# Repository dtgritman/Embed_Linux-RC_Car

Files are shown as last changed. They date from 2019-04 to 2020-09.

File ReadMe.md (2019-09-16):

# Humans vs Zombies

### Team
 * **Miguel**: Building a vehicle to hold the project components.
 * **Dustin**: Building a nerf cannon that will angle up/down and rotate side to side. 
 * **Faizan**: Creating the object detection mechanism to target objects.

### Goal
 We plan to create a vehicle which shoots nerf projectiles for the campus-wide game called ‘Humans vs. Zombie’. Our tank has two hardware modules, the tanks enclosure and the nerf cannon used to fire the nerf pelts. We hope to add object recognition to our project to make it autonomous We will not only be using the Pi’s onboard GPIO pins but use a server to stream any video information onto a web-server. The Pi will also log anyone it deems to be threatening for correction or algorithm calibration.

# Tutorial 
Each part has its respective tutorial due to the modulization of the project. Please follow each markdown file closely and 

## Pi Setup

You can find a full tutorial in the [`setup/`](/setup/rasp_pi.md) folder

## Part 1 (Car Setup)

#### Modifications

1. Removing the top of the car 
2. Removing the cars microprocessor
3. Resoldering the on/off switch 

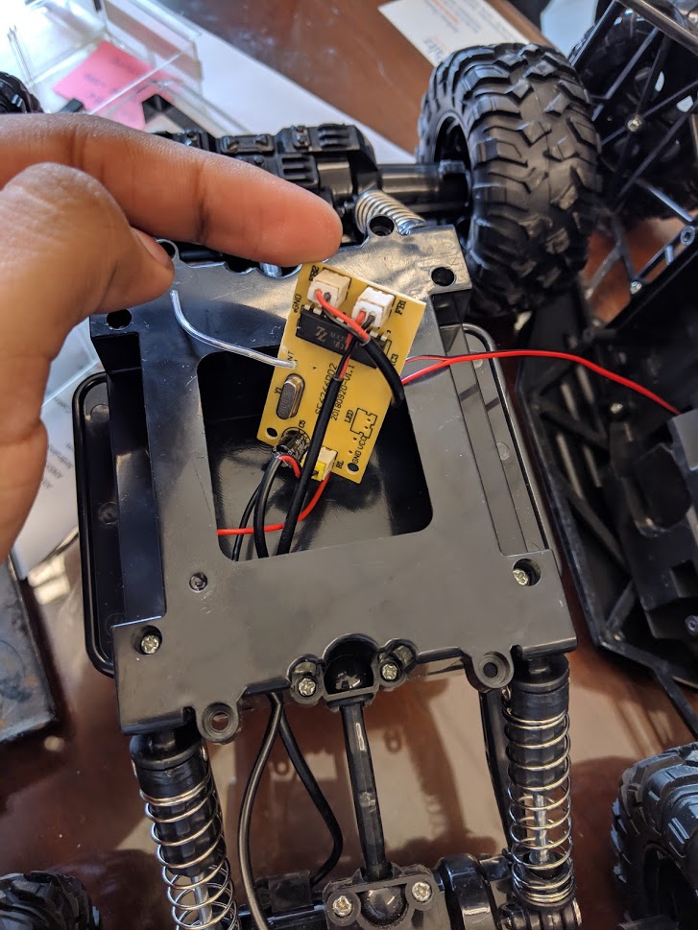
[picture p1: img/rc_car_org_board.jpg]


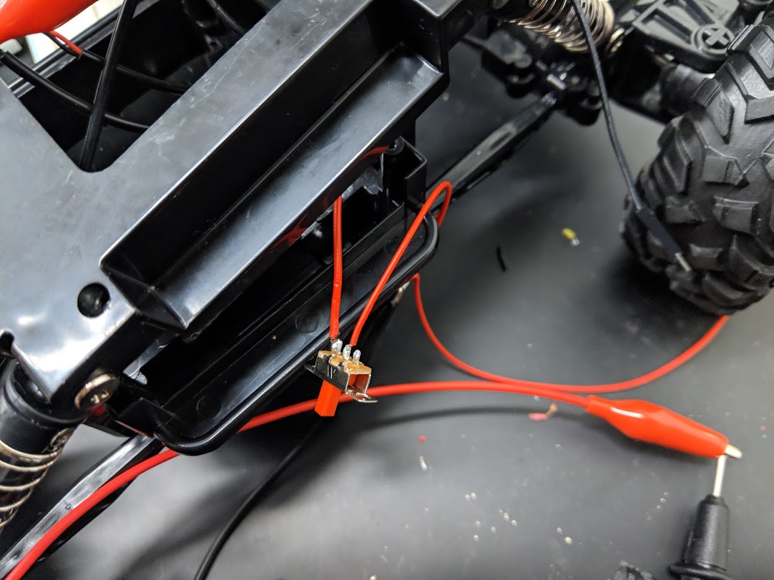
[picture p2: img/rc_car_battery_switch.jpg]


#### Wiring 

    STBY = GPIO #17     = Stand By

    Drive motor:
    PWMA = GPIO #3      = Speed
    AIN2 = GPIO #4
    AIN1 = GPIO #18

    Left-Right controller:
    BIN1 = GPIO #27
    BIN2 = GPIO #23    
    PWMB = GPIO #24    = Speed

## Part 2 (Nerf Module Setup)

Though this part can be completed without setting up the car we highly recommend finishing the car set-up for any changes you may need to make.

### Assembly of Cannon
#### Parts Needed
- Stepper Motor (NEMA 17)
- Standard 180 degree Servo Motor
- 1x Bearing (for the top stand center) with an inner diamter of 12mm, an outer diameter of 37mm, and a width of 12mm.
- 2x Bearings (for arm mounts) with an inner diameter of 7mm, outer diameter of 19mm, and a width of 6mm.
- 4x Transfer Ball bearings (for the legs of the top) with a bearing surface that has a diameter of 15mm and a mounting cylinder with a diameter of 25mm which has a flared top.

#### Stand Assembly
1. Sand the bearing mounting hole at the top of the arm until you can press in the bearing using a tool like a c-clamp (the bearing should not be able to be inserted by hand).
2. Once the bearing is mounted, insert the ArmAxle in to the bearing (some sanding may be required), this should be very difficult to insert and can be tapped in very lightly with a hammer.
3. With the ArmAxle mounted, you can place the ArmGear on the side with the stepper motor mount. This gear should be relatively difficult to push on the axle.
4. Place the stepper motor on the mount and screw it down but leave enough slack to slide the motor up and down.
5. Put the StepperGear on the motor and place it so the gears are in contact (leave a very small amount of space so the gears don't bind).
6. Push the LaserBracket on to the Axle (should be relatively snug).
7. Finally with the laser pointer mounted on the LaserRail, slide the rail in to the bracket (again this should be relatively snug).

#### Base Assembly
1. The base has raised wall which will be used to mount the ssd and raspberry pi, to do so we used velcro on the inner wall and ssd to mount it and on the outer wall we used neoprene closed cell foam to help hold the raspberry pi (and prevent damage to the pins) with rubber bands wrapped around.
2. With the bearing track sanded down, place the BaseGear on the center rod (should fit snuggly).

#### Top Assembly
1. First, press in the center bearing.
2. Attach the ServoGear to servo, we used hot glue on a servo horn (if using this method make sure its centered).
3. Mount the servo to the top using the ServoMounts (slowly screw the screws in, taking breaks frequently so you don't break screw).
4. Place the Transfer Ball Bearings in to the tops four arms (should fit snuggly).
5. Mount the stand(s) to the top using the ArmBrackets and ArmMounts (carefully screw in to the mounting holes).
6. Finally place the top on the base and press the top down so the base rod snuggly fits in the bearing and then place a screw through the TopBearingWasher and screw in to the rod to prevent the top from lifting off the base.

## Part 3 (Object Detection)

Our project uses OpenCV and python3 to detect human faces. We are using precompiled libraries. 
[Object Detection](/setup/object_detection.md)

## Part 4 (Putting it all together)

You can find our master init file in the [code/](https://github.com/MiguelAPerez/Humans-vs-Zombies/tree/master/code) folder. To run the RC Car run the `web.py` file using python3 

```bash
 $ python3 web.py
```

#### Citation 
 Cascade Used: [Opencv git repo](https://github.com/opencv/opencv/blob/master/data/haarcascades/haarcascade_frontalcatface.xml)

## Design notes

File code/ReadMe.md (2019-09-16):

## This folder contains all the code related to the project

All Pin values can be found in the `web.py` file

| File | Description |
|---|---|
| [Drone/Cannon.py](Drone/Cannon.py) | This file contains the TankCannon class and StepperMotor class which can be used to control the tanks cannon by turning it left, right, up, and down, and turning the cannon on and off. |
| [Drone/Car.py](Drone/Car.py) | This file contains the Car class which can be used to control the rc car drive and steering with speed control. |
| [web.py](web.py) | This program contains the webserver for the project which controls the tank. It uses Flask on port 8080. This also contains the detection code to run by itself. |
| [tankps4.py](tankps4.py) | This program can be used to control the tank with ps4 controller. (L2/R2 for drive, left joystick for steering, right joystick for cannon position, R1 for firing, and options to pause/resume) |
|[camera.py](camera.py)| Class for the video stream and object detection|

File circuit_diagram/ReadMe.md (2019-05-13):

# This directory contains the circuit diagrams for the car and the cannon

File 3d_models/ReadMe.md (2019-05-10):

# This directory has all the 3d models created and used for the project.
| 3D File | Notes |
| --- | ----- |
| [Arm.stl](Arm.stl) | The support arm (without a motor mount), will act as a support to help keep the nerf gun level with a bearing hole that fits an axle. |
| [ArmAxle.stl](ArmAxle.stl) | The axle connects the stands to the nerf gun mounting brackets (or laser mounting bracket), so they can rotate freely in a bearing. |
| [ArmAxleGear.stl](ArmAxleGear.stl) | This gear fits on the arm axle to mesh with the steppergear. |
| [ArmStand.stl](ArmStand.stl) | This stand has two sides that clamp the arms to hold them in place and connect them to the top. |
| [ArmStandMount.stl](ArmStandMount.stl) | This mount has holes and goes on the underside of the top for the arm stands to screw in. |
| [ArmStepper.stl](ArmStepper.stl) | The stepper arm for the nerf gun stand has a mount for the stepper motor (which will have a gear) and a hole for the axle bearing and the axle (which will also have a gear) to attach to the bracket of the nerf gun (or laser pointer) so the cannon can rotate. |
| [ArmStepperGear.stl](ArmStepperGear.stl) | This gear will slide on to the stepper motor and mesh with the axle gear to rotate the cannon. |
| [Base.stl](Base.stl) | The base will have the top slid on to rotate in the track. |
| [BaseGear.stl](BaseGear.stl) | This gear will be slid on the center pole to mesh with the servo gear. |
| [LaserMount.stl](LaserMount.stl) | The laser pointer will be connected to this mount. |
| [LaserMountBracket.stl](LaserMountBracket.stl) | The laser pointer mount will connect to this bracket which will connect to the arm axle. |
| [ServoGear.stl](ServoGear.stl) | This gear will be put on the servo horn and mesh with the base gear to rotate the top. |
| [ServoMount.stl](ServoMount.stl) | This mount goes on the top of the top and will have the servo screwed in. |
| [Top.stl](Top.stl) | The top will have the servo and arms mounted on it and then will be mounted to the base. |
| [TopBearingWasher.stl](TopBearingWasher.stl) | The washer will go between the center bearing in the top and the screw that will screw in to the base. |

## Extra Notes
##### - All 3D files were printed using a Standard Prusa i3 MK3 with the settings in Prusa Control of Detail: 0.1mm and Infill: around 20%
##### - Some sanding of parts will be required for them to fit together properly \*\*becareful not to remove too much material. They must fit snuggly\*\*

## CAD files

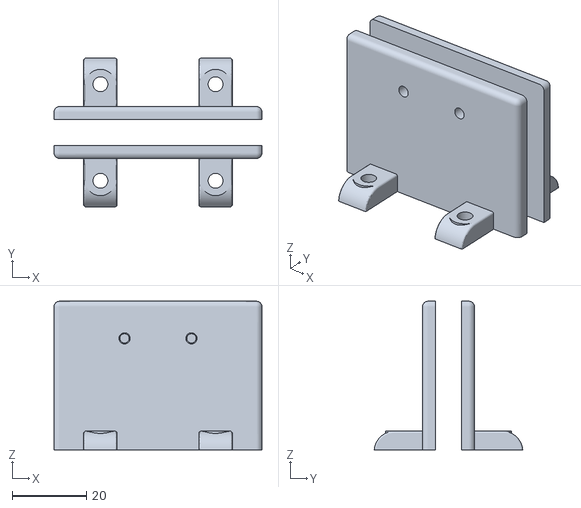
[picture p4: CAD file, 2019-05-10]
3d_models/ArmStand.stl
56.0 x 40.0 x 40.0

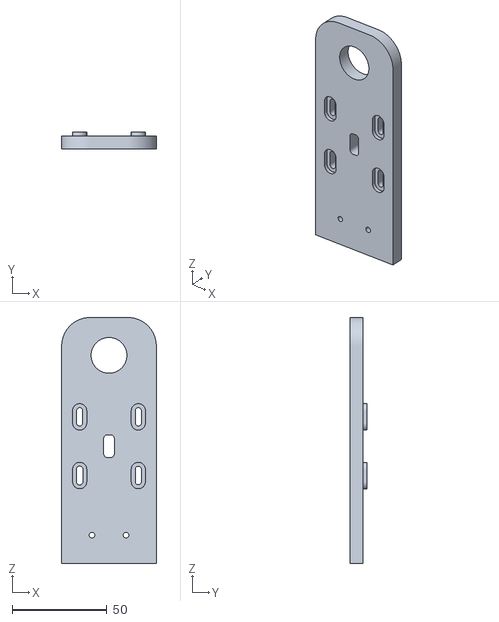
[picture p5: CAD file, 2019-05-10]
3d_models/ArmStepper.stl
50.0 x 9.00 x 130.0

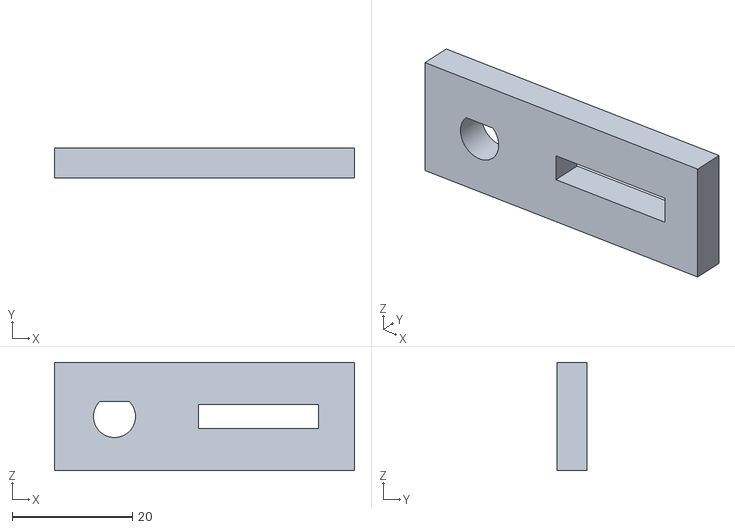
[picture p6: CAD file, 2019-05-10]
3d_models/LaserMountBracket.stl
50.0 x 5.00 x 18.0

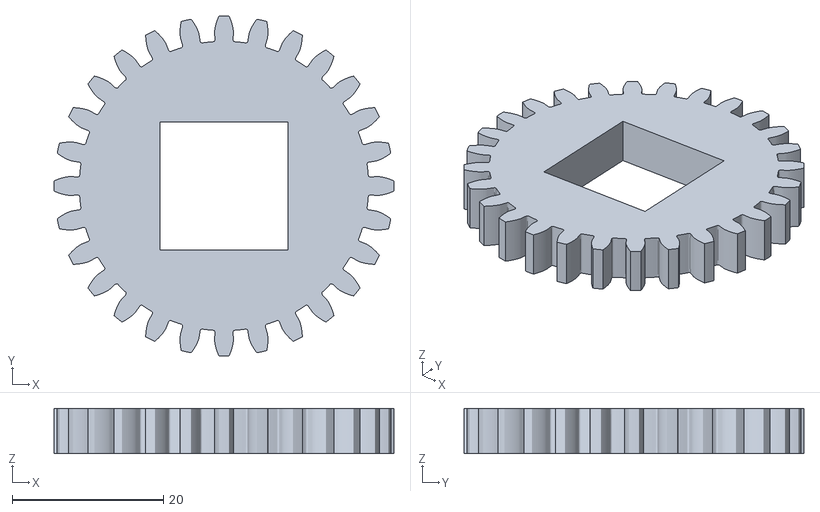
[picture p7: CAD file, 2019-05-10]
3d_models/BaseGear.stl
45.0 x 45.0 x 6.00

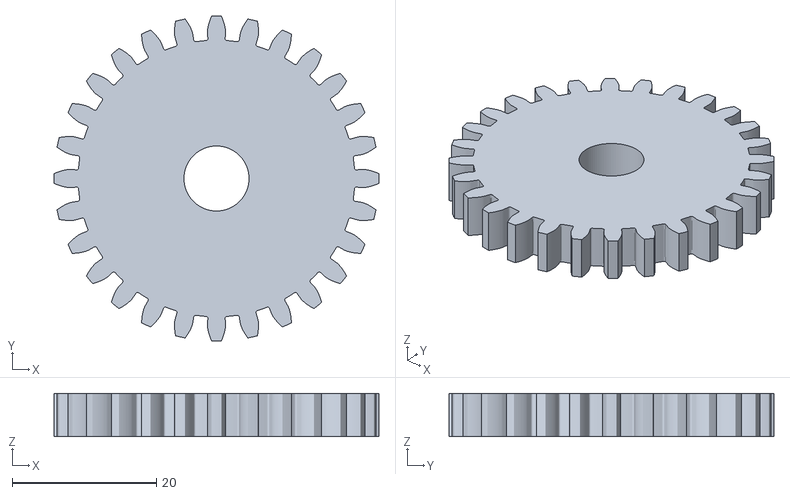
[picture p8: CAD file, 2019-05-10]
3d_models/ServoGear.stl
45.0 x 45.0 x 6.00

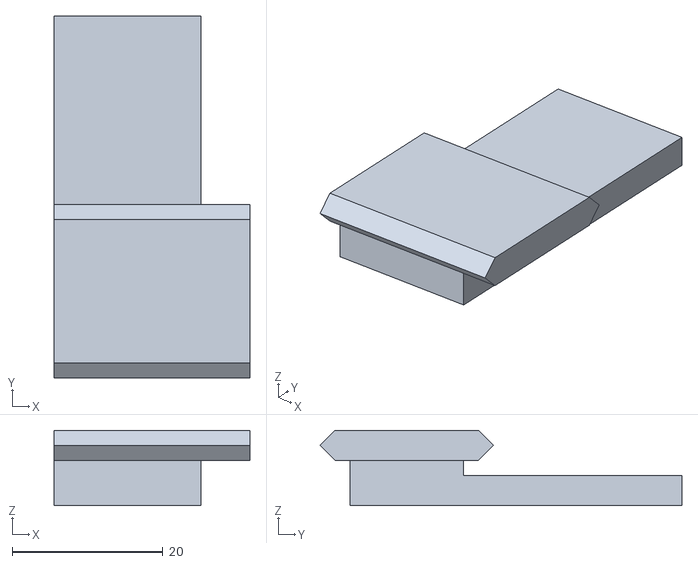
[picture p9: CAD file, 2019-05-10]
3d_models/LaserMount.stl
26.0 x 48.0 x 10.0

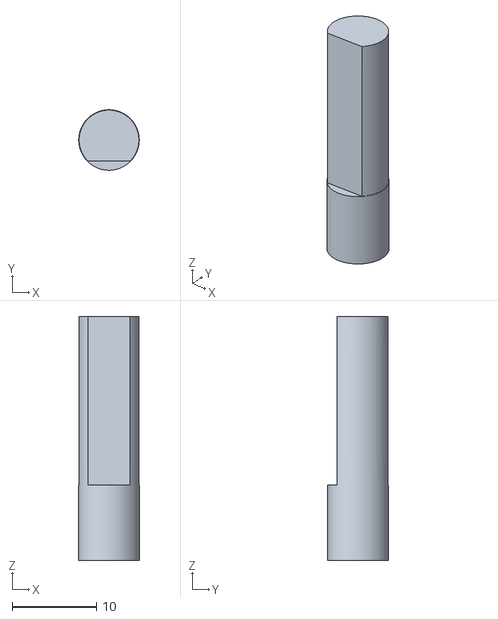
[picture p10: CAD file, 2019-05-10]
3d_models/ArmAxle.stl
7.20 x 7.20 x 29.0

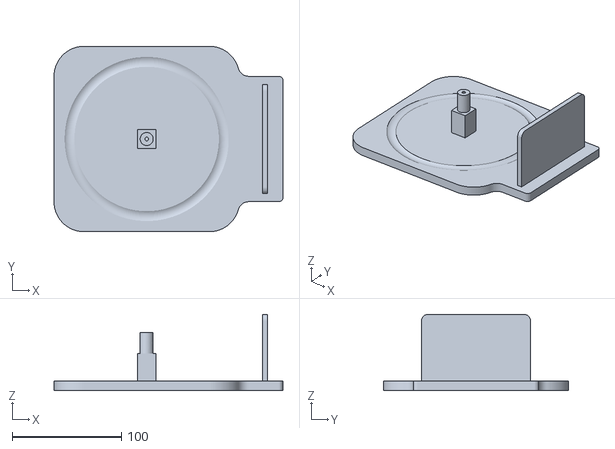
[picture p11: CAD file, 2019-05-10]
3d_models/Base.stl
210.0 x 170.0 x 70.0

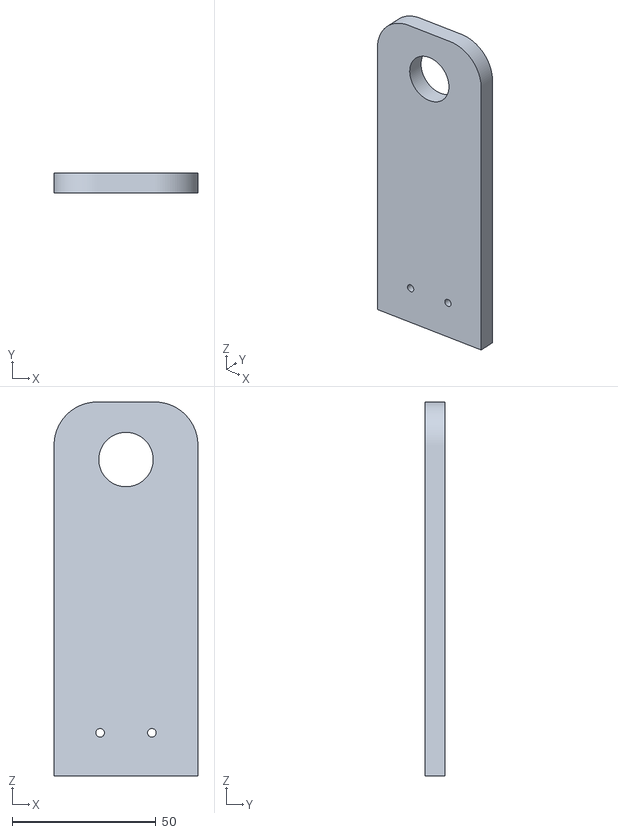
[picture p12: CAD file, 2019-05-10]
3d_models/Arm.stl
50.0 x 7.00 x 130.0

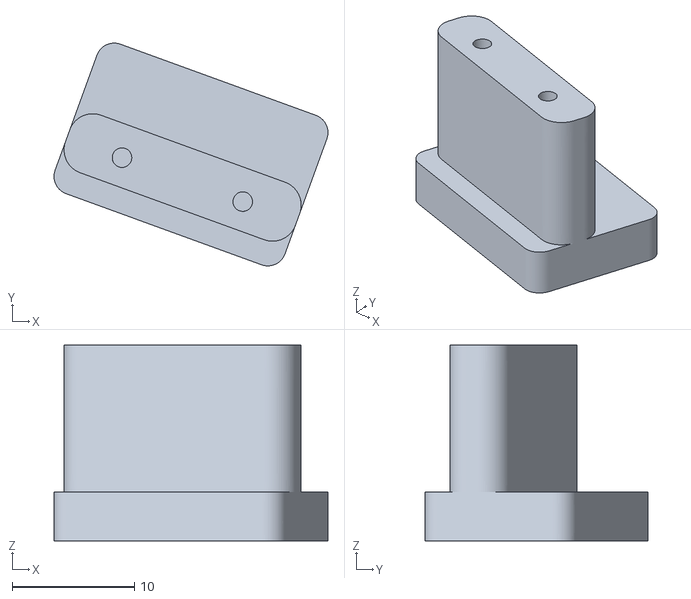
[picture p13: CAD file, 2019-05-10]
3d_models/ServoMount.stl
22.4 x 18.2 x 16.0

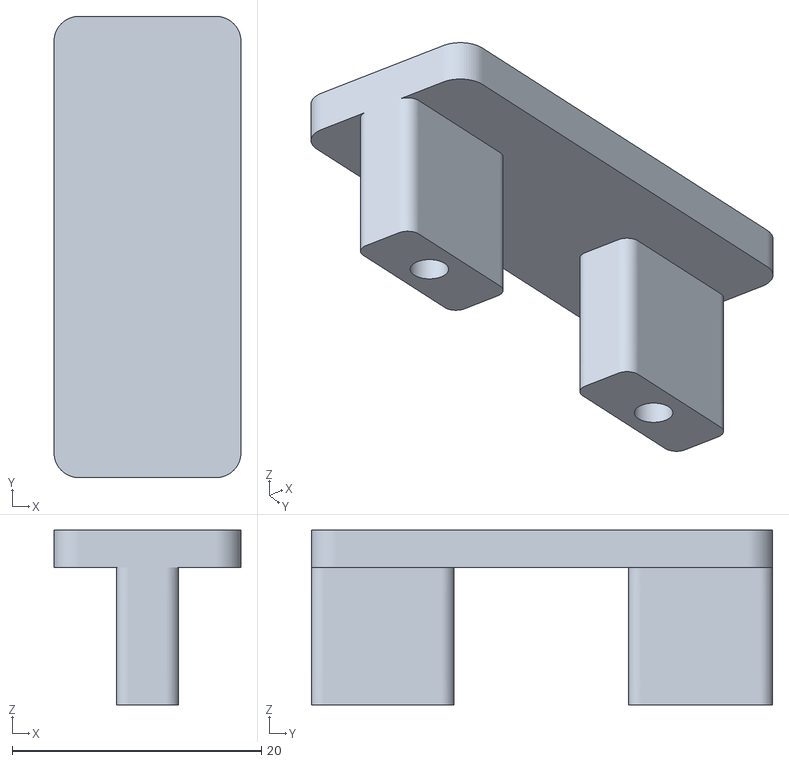
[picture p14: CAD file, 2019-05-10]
3d_models/ArmStandMount.stl
15.0 x 37.0 x 14.0

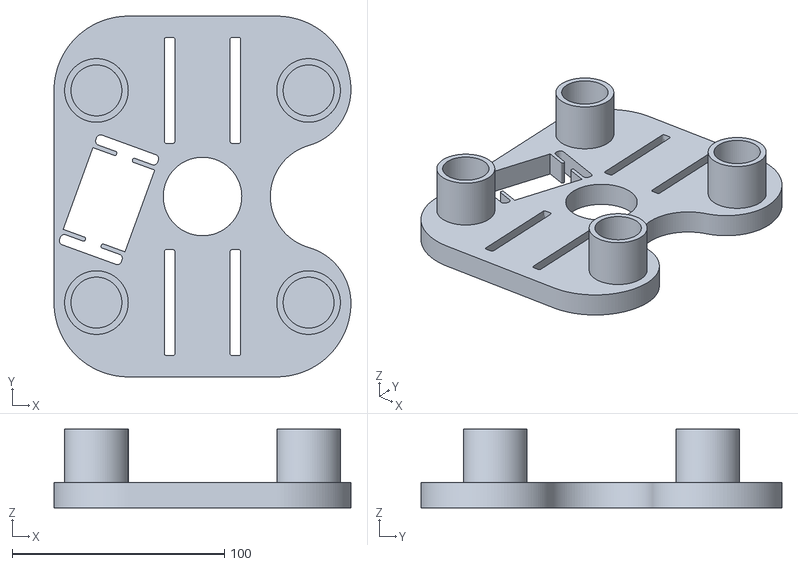
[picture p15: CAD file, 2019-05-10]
3d_models/Top.stl
140.0 x 170.0 x 37.0

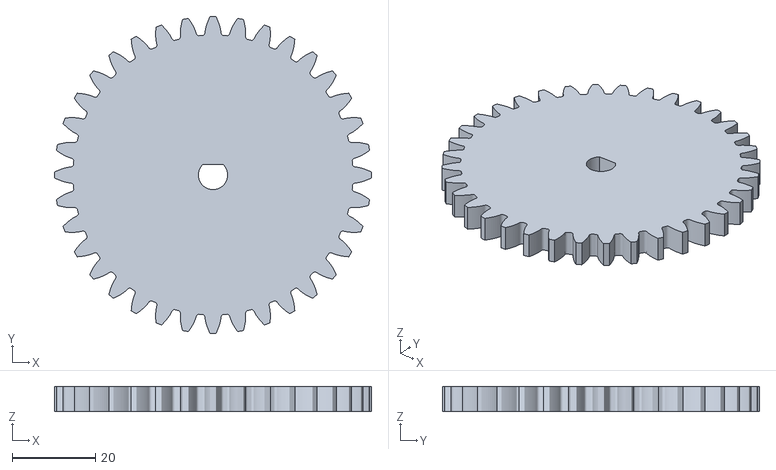
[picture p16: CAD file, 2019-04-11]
3d_models/ArmAxleGear.stl
76.0 x 76.0 x 6.00

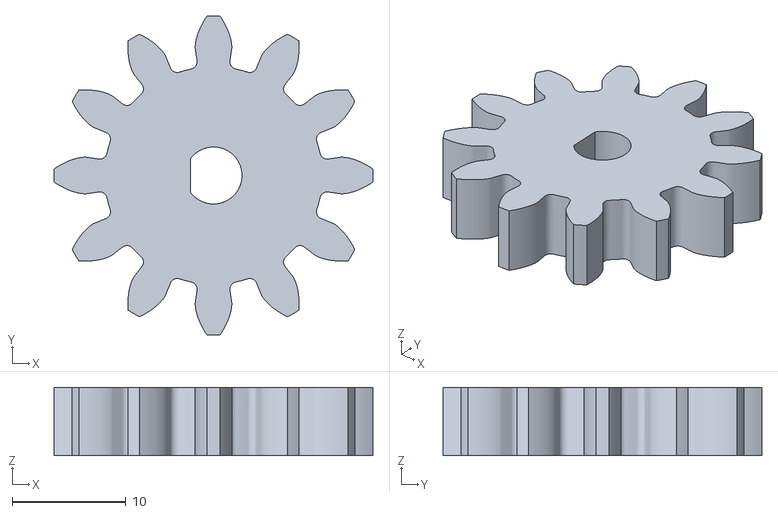
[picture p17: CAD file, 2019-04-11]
3d_models/ArmStepperGear.stl
28.0 x 28.0 x 6.00

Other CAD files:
3d_models/TopBearingWasher.stl

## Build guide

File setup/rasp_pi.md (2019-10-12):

## Setup 

Each part of the project is modularised for efficiency and fault prevention. This means each part (the nerf_module object_detection and rc_car) can work as a standalone part.  

### Raspberry Pi - Setup

Note that to execute these commands you need to open the terminal by finding it in the programs menu or by connecting a keyboard to the raspberry pi and pressing CTRL + ALT + T

Terminal- interface which lets you enter commands to perform tasks
sudo- command which gives a user more access to critical system files (equivalent of administrator privilages on Windows)
apt- the program that manages programs, allows you to install and remove programs
OpenCV- set of tools which allow you to work with videos and images, applications include facial recognition
Web server- computer which serves a web page to anyone connecting to it through the internet
Daemon- program that runs in the background
Static IP- IP address that does not change

##### Required Dependencies  
**Note:** You will need to have installed Raspbian or Raspbian Lite on your Pi.
If you don't know how to, follow the tutorial on the [Raspberry Pi Foundation's website](https://www.raspberrypi.org/documentation/installation/installing-images/)

The webserver uses flask. If it's not already installed the in can be installed with:  
```bash
$ sudo apt-get install python3-flask
```  
The tank control classes use pigpio to control the gpio. This library has better PWM signal control than RPi. To install this library use:  
```bash
$ sudo apt-get install pigpio python3-pigpio
```
This library requires the pigpio daemon to be running. This daemon can be started manually (only needs to be started once each boot) using:
```bash
$ sudo pigpiod
```
or it can be set to run on system boot with:
```bash
$ sudo systemctl enable pigpiod
$ sudo reboot
```

#### Hotspot Setup
We wanted to not be reliant on a router to connect to our Pi so we turned it into a hotspot to connect to it without our home or school wifi.

##### Access point in a standalone network (NAT)
**Note**: This is a short version of the raspberrypi.org tutorial. More information, it can be found [here](https://www.raspberrypi.org/documentation/configuration/wireless/access-point.md)

##### 1. Installs
Update your Pi
```bash
$ sudo apt-get update
$ sudo apt-get upgrade
```

Install all the required software:

```bash
$ sudo apt-get install dnsmasq hostapd
```

Turn the new software off as follows:
```bash
$ sudo systemctl stop dnsmasq
$ sudo systemctl stop hostapd
```

To ensure that an updated kernel is configured correctly after install, reboot:
```bash
$ sudo reboot 
```

##### 2. Configuring a static IP

This documentation assumes that we are using the standard 192.168.x.x IP addresses for our wireless network, so we will assign the server the IP address 192.168.4.1. It is also assumed that the wireless device being used is **wlan0**.

To configure the static IP address, edit the dhcpcd configuration file with:
```bash 
$ sudo nano /etc/dhcpcd.conf
```

Go to the end of the file and edit it so that it looks like:

```
interface wlan0
    static ip_address=192.168.4.1/24
    nohook wpa_supplicant
```
Now restart the dhcpcd daemon and set up the new wlan0 configuration:

```bash
$ sudo service dhcpcd restart
```
##### 3. Configuring the DHCP server (dnsmasq)

The DHCP service is provided by dnsmasq. By default, the configuration file contains a lot of information that is not needed, and it is easier to start from scratch. Rename this configuration file, and edit a new one:

```bash 
$ sudo mv /etc/dnsmasq.conf /etc/dnsmasq.conf.orig  
$ sudo nano /etc/dnsmasq.conf
```

Type or copy the following information into the dnsmasq configuration file and save it:
```
interface=wlan0      # Use the require wireless interface
  dhcp-range=192.168.4.2,192.168.4.20,255.255.255.0,24h
```
So for **wlan0**, we are going to provide IP addresses between 192.168.4.2 and 192.168.4.20, with a lease time of 24 hours. If you are providing DHCP services for other network devices (e.g. eth0), you could add more sections with the appropriate interface header, with the range of addresses you intend to provide to that interface.

##### 4. Configuring the access point host software (hostapd)

You need to edit the hostapd configuration file. After initial install, this will be a new/empty file.

```bash
$ sudo nano /etc/hostapd/hostapd.conf
```
Add the information below to the configuration file. This configuration assumes we are using channel 7, with a network name of **HumanVsZombies**, and a password **letmeinrightnow**. Note that the name and password should not have quotes around them. The passphrase should be between 8 and 64 characters in length.

```
interface=wlan0
driver=nl80211
ssid=HumanVsZombies
hw_mode=g
channel=7
wmm_enabled=0
macaddr_acl=0
auth_algs=1
ignore_broadcast_ssid=0
wpa=2
wpa_passphrase=letmeinrightnow
wpa_key_mgmt=WPA-PSK
wpa_pairwise=TKIP
rsn_pairwise=CCMP
```
We now need to tell the system where to find this configuration file.

```bash 
$ sudo nano /etc/default/hostapd
```
Find the line with #DAEMON_CONF, and replace it with this:
```
DAEMON_CONF="/etc/hostapd/hostapd.conf"
```

**Now start up the remaining services:**

```bash
$ sudo systemctl start hostapd
$ sudo systemctl start dnsmasq
```

**NOTE:** if sudo systemctl start hostapd fails to start and is masked you should use these commands to fix the issue:
```bash
$ sudo systemctl unmask hostapd
$ sudo systemctl enable hostapd
$ sudo systemctl start hostapd
```

**Add routing and masquerade**

Edit /etc/sysctl.conf and uncomment this line:

```
net.ipv4.ip_forward=1
```

Add a masquerade for outbound traffic on eth0:
```bash
$ sudo iptables -t nat -A  POSTROUTING -o eth0 -j MASQUERADE
```
Save the iptables rule.
```bash
$ sudo sh -c "iptables-save > /etc/iptables.ipv4.nat"
```
Edit _**/etc/rc.local**_ and add this just above **"exit 0"** to install these rules on boot.
```
iptables-restore < /etc/iptables.ipv4.nat
```
**Reboot**

The network SSID you specified in the hostapd configuration should now be present, and it should be accessible with the specified password.

If SSH is enabled on the Raspberry Pi access point, it should be possible to connect to it from another Linux box (or a system with SSH connectivity present) as follows, assuming the pi account is present:
```bash
$ ssh pi@192.168.4.1
```
By this point, the Raspberry Pi is acting as an access point, and other devices can associate with it. Associated devices can access the Raspberry Pi access point via its IP address for operations such as rsync, scp, or ssh.

#### Potental Error
If you are having an issue with logging into the wifi you need to manually set you the ipv4 password.

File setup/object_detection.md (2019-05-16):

# Current OpenCV Install Method

## OpenCV 3.4.4 was used

### Installation Process

##### Required Dependencies  
Install picamera and pip3 using apt-get:  
```
~$ sudo apt-get install python3-picamera python3-pip
```

With pip3 installed, use pip3 to install opencv-contrib-python and imutils  
```
~$ pip3 install opencv-contrib-python imutils
```

This opencv installation may look for some libraries that are not installed, to install these commonly missing libraries run this command:
```
~$ sudo apt install libhdf5-100 libsz2 libharfbuzz0b libatlas3-base libwebp6 libtiff5 libjasper1 libilmbase12 libopenexr22 libgstreamer1.0-0 libavcodec57 libavformat57 libswscale4 libqtgui4 libqt4-test
```

# Previous OpenCV Install Method

## Compiling OpenCV 3.4.1 on a Raspberry pi

### Step 1: Extend your disk before proceeding

    $ sudo raspi-config

Go to "Advanced Options"
Select "Expand Filesystem", hit enter
Reboot your pi:

    $ sudo reboot

### Step 2: Reclaim space by removing LibreOffice and Wolfram Engine

    $ sudo apt-get purge wolfram-engine
    $ sudo apt-get purge libreoffice*
    $ sudo apt-get clean
    $ sudo apt-get autoremove

### Step 3: Install dependencies

    $ sudo apt-get update && sudo apt-get upgrade
    $ sudo apt-get install build-essential cmake pkg-config
    $ sudo apt-get install libjpeg-dev libtiff5-dev libjasper-dev libpng12-dev
    $ sudo apt-get install libavcodec-dev libavformat-dev libswscale-dev libv4l-dev
    $ sudo apt-get install libxvidcore-dev libx264-dev
    $ sudo apt-get install libgtk2.0-dev libgtk-3-dev
    $ sudo apt-get install libcanberra-gtk*
    $ sudo apt-get install libatlas-base-dev gfortran
    $ sudo apt-get install python2.7-dev python3-dev

    # Installs pip and NumPy
    $ wget https://bootstrap.pypa.io/get-pip.py
    $ sudo python get-pip.py
    $ pip install numpy

### Step 4: Download the OpenCV Source Code

    $ cd ~
    $ wget -O opencv.zip https://github.com/opencv/opencv/archive/3.4.1.zip
    $ unzip opencv.zip
    $ wget -O opencv_contrib.zip https://github.com/opencv/opencv_contrib/archive/3.4.1.zip
    $ unzip opencv_contrib.zip

### Step 5: Increase size of swap file

    $ sudo nano /etc/dphys-swapfile

    # change the CONF_SWAPSIZE to 1024 from 100
    CONF_SWAPSIZE=1024

**Note:** Undo this setting once the compile is complete 

**Back up your SD Card, as increasing the size of the swap file will shorten the lifespan of your SD Card and can potentially corrupt it as well**

Restart the swap service

    $ sudo /etc/init.d/dphys-swapfile stop
    $ sudo /etc/init.d/dphys-swapfile start

### Step 6: Compile and install optimized OpenCV

    $ cd ~/opencv-3.4.1/
    $ mkdir build
    $ cd build
    $ cmake -D CMAKE_BUILD_TYPE=RELEASE \
        -D CMAKE_INSTALL_PREFIX=/usr/local \
        -D OPENCV_EXTRA_MODULES_PATH=~/opencv_contrib-3.4.1/modules \
        -D ENABLE_NEON=ON \
        -D ENABLE_VFPV3=ON \
        -D BUILD_TESTS=OFF \
        -D INSTALL_PYTHON_EXAMPLES=OFF \
        -D BUILD_EXAMPLES=OFF ..
    $ sudo make -j4

If you encounter any issues while compiling, run

    $ sudo make clean
    $ sudo make

Remember to restore the swap size back to 100 and restart the swap service

### Step 7: Install the build

    $ sudo make install
    $ sudo ldconfig
    $ sudo nano /etc/ld.so.conf.d/opencv.conf

Add the following line to opencv.conf

    /usr/local/lib          # enter this in opencv.conf, NOT at the command line
                            (leave a blank line at the end of opencv.conf)
Save and exit by hitting CTRL+X, Y and then ENTER

    $ sudo ldconfig
    $ sudo nano /etc/bash.bashrc

add the following lines at the bottom of bash.bashrc

    PKG_CONFIG_PATH=$PKG_CONFIG_PATH:/usr/local/lib/pkgconfig
    export PKG_CONFIG_PATH

(leave a blank line at the end of bash.bashrc)

Save and exit (CTRL+X, Y and then ENTER)

### Step 8: Reboot and verify installation

    $ sudo reboot
    $ python
    >>> import cv2
    >>> print cv2.__version__
The output should be

    '3.4.1'

### Done

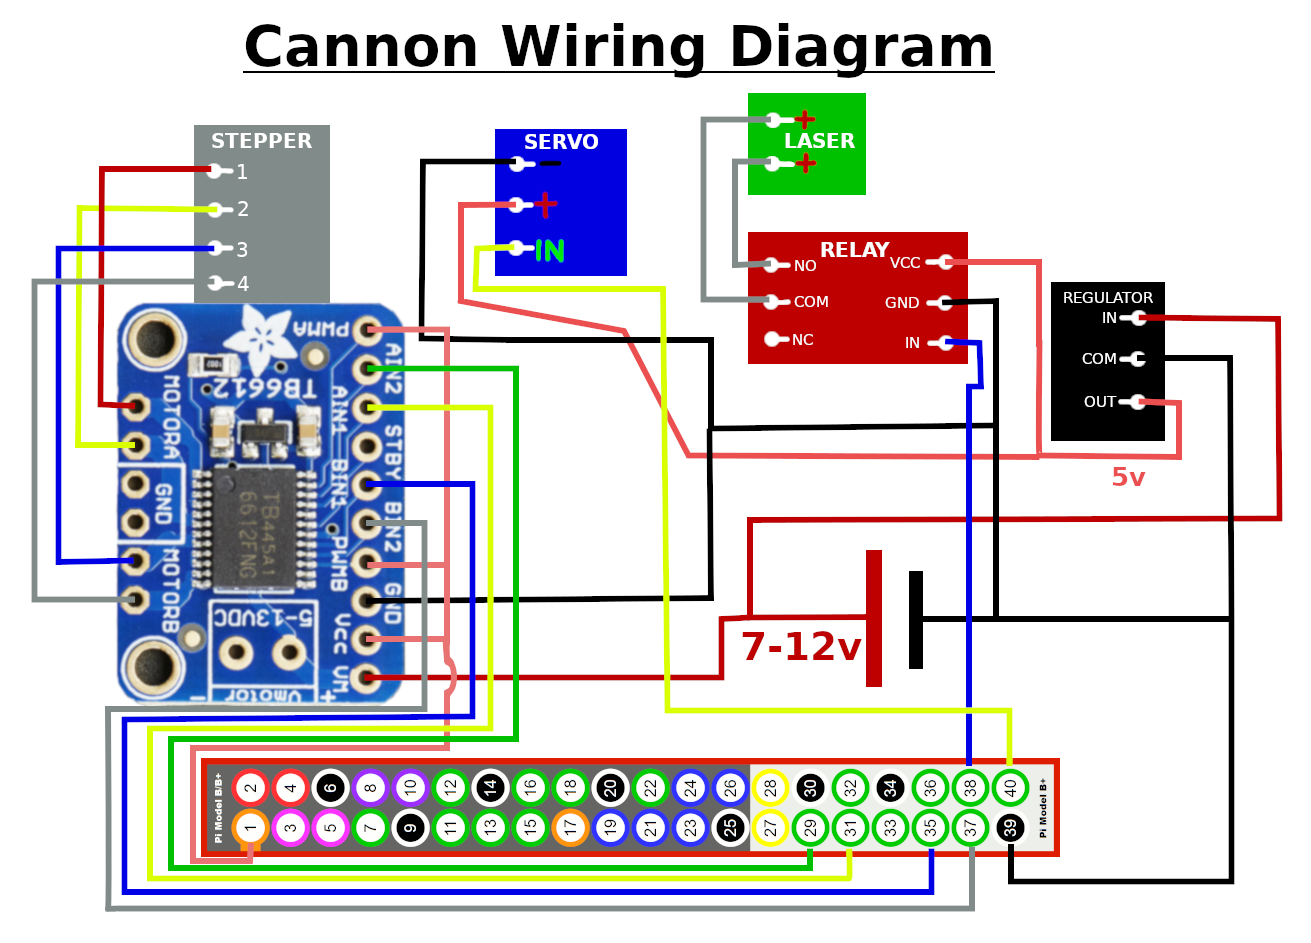
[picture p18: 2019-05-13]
circuit_diagram/CannonWiringDiagram.png

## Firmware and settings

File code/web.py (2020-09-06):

# imports
from flask import Flask, render_template, request, Response
from threading import Thread
import sqlite3 as sqlite
import json
import time
import cv2
import numpy as np
import imutils
import os

# import custom car classes
from camerapi import VideoCamera
from Drone.Cannon import TankCannon, StepperMotor
from Drone.Car import Car

# tank starts actived and in manual mode
tankActive = 1
autoActive = 0
streamFrame = None
streamActive = True

# cannon gpio pins and intialization
pinCannon = 20
pinServo = 21
stepperAIN2 = 5
stepperAIN1 = 6
stepperBIN1 = 19
stepperBIN2 = 26
cannon = TankCannon(pinCannon, pinServo, StepperMotor(stepperAIN1, stepperAIN2, stepperBIN1, stepperBIN2), stepper_GearRatio=3, rotationServo_Offset=50)

# car gpio pins and intialization
carSTBY = 17
carPWMA = 3
carAIN2 = 4
carAIN1 = 18
carBIN1 = 27
carBIN2 = 23
carPWMB = 24
# car distance sensors gpio pins
distanceTrig = 22
distanceEchoL = 9
distanceEchoF = 11
distanceEchoR = 10
car = Car(carSTBY, carPWMA, carAIN2, carAIN1, carBIN1, carBIN2, carPWMB, distanceTrig, [distanceEchoL, distanceEchoF, distanceEchoR])



videoFeed = VideoCamera()

app = Flask(__name__)

@app.route('/')
def index():
    global tankActive, autoActive
    tankActive = 1
    autoActive = 0
    cannon.activate()
    car.activate()
    return render_template('index.html')

# get the camera feed output
def gen():
    global streamFrame, streamActive
    frame = open('static/img/loading.jpg', 'rb').read()
    while streamActive:
        if streamFrame != None:
            frame = streamFrame
        
        yield (b'--frame\r\n'
                b'Content-Type: image/jpeg\r\n\r\n' + frame + b'\r\n\r\n')
    
    return ""

@app.route('/videofeed')
def video_feed():
    return Response(gen(videoFeed), mimetype='multipart/x-mixed-replace; boundary=frame')

@app.route('/mask', methods=['POST'])
def mask():
    return Response(gen(), mimetype='multipart/x-mixed-replace; boundary=frame')

@app.route('/detectionlogs')
def detectionLogJSON():
    try:
        # connect to DetectionLog Database
        con = sqlite.connect('../log/DetectionLogDB.db')
        cur = con.cursor()
        
        # store all the rows in the DetectionLog table in an array
        detectionLogArray = []
        for row in cur.execute("SELECT * FROM DetectionLogs ORDER BY Datetime(Date) DESC LIMIT 20;"):
            detectionLogArray.insert(0, { "Date": row[0], "Type": row[1], "Image": row[2] })
        
        # output array as JSON for the client to use
        return json.dumps(detectionLogArray)
    
    except sqlite.Error as e:
        print("Error %s:" % e.args[0])
        return

@app.route('/tankactive', methods=['POST'])
def tankActive():
    global tankActive
    tankActive = int(request.form['tankActive'])
    if tankActive:
        cannon.activate()
        car.activate()
    else:
        cannon.deactivate()
        car.deactivate()
    
    return ""

@app.route('/autoactive', methods=['POST'])
def autoActive():
    global autoActive
    autoActive = int(request.form['autoActive'])
    
    return ""

@app.route('/carcontrol', methods=['POST'])
def carControl():
    global tankActive, autoActive
    if not tankActive:
        return ""
    
    # -1 = left, 0 = off, 1 = right
    steerDir = 0
    # steering motor speed percent
    steerPerc = int(request.form['steering'])
    if steerPerc > 0:
        steerDir = 1
    elif steerPerc < 0:
        steerDir = -1
        steerPerc = -steerPerc
    
    car.setSteering(steerDir, steerPerc)
    
    # -1 = reverse, 0 = off, 1 = forward
    driveDir = 0
    # drive motor speed percent
    drivePerc = int(request.form['drive'])
    if drivePerc > 0:
        driveDir = 1
    elif drivePerc < 0:
        driveDir = -1
        drivePerc = -drivePerc
    
    car.setDrive(driveDir, drivePerc)
    
    return ""

@app.route('/cannoncontrol', methods=['POST'])
def cannonControl():
    global tankActive, autoActive
    if not tankActive or autoActive:
        return ""
    
    canState = int(request.form['cannonState'])
    cannon.fireCannon(canState)
    
    baseAngle = int(request.form['cannonBaseAngle'])
    cannon.setBaseRotation(baseAngle)
    
    canAngle = int(request.form['cannonAngle'])
    cannon.setCannonAngle(canAngle)
    
    return ""

# the threaded function that runs the camera and the auto mode
def runAutoDetection():
    global tankActive, autoActive, streamFrame, streamActive
    tankActive = 1
    autoActive = 0
    streamActive = True
    camera = VideoCamera()
    
    # setup connection to DetectionLog Database
    con = sqlite.connect('../log/DetectionLogDB.db')
    cur = con.cursor()
    logPictureNum = 0
    
    # find current picture number to start at
    while os.path.exists('static/img/image%s.jpg' % logPictureNum):
        logPictureNum += 1
    
    prevDetectCoords = [0, 0]
    
    while streamActive:
        # get the current frame and detection coords
        streamImage, detectCoords = camera.get_frame()
        ret, jpeg = cv2.imencode('.jpg', streamImage)
        streamFrame = jpeg.tobytes()
        
        # don't control the car/cannon when in manual mode
        if not tankActive or not autoActive:
            continue
        
        car.updateDistances()
        print("Distances: %s" % car.distances)
        
        # check if something is detected
        if detectCoords[0] > -1:
            # check for large movements of the center of the box, to indicate unique target for logging
            if abs(detectCoords[0] - prevDetectCoords[0]) > 30 or abs(detectCoords[1] - prevDetectCoords[1]) > 30:
                cv2.imwrite('static/img/image%s.jpg' % logPictureNum, streamImage, [cv2.IMWRITE_JPEG_QUALITY, 90])
                # log the timestamp, detection type, and image to SQLite db
                current_time = time.strftime("%Y-%m-%d %H:%M:%S")
                detection_type = "unknown"
                image_name = ("image%s.jpg" % logPictureNum)
                cur.execute('INSERT INTO DetectionLogs(Date, Type, Image) VALUES (?,?,?);', (current_time, detection_type, image_name))
                con.commit()
                logPictureNum += 1
            
            cannon.setCannonPos(detectCoords[0], detectCoords[1], camera.resolution[0], camera.resolution[1])
            cannon.fireCannon(1)
            # store the detection coordinates for reference later
            prevDetectCoords = detectCoords
        else:
            cannon.fireCannon(0)


if __name__ == '__main__':
    t1 = Thread(target = runAutoDetection)
    t1.setDaemon(True)
    t1.start()
    app.run(host='0.0.0.0', port=8080, threaded=True)
    streamActive = False

print("Exiting...")
cannon.stop()
car.stop()

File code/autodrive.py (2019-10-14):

import time
from Drone.Car import Car

# car gpio pins and intialization
carSTBY = 17
carPWMA = 3
carAIN2 = 4
carAIN1 = 18
carBIN1 = 27
carBIN2 = 23
carPWMB = 24
# car distance sensors gpio pins
distanceTrig = 22
distanceEchoL = 9
distanceEchoF = 11
distanceEchoR = 10
car = Car(carSTBY, carPWMA, carAIN2, carAIN1, carBIN1, carBIN2, carPWMB, distanceTrig, [distanceEchoL, distanceEchoF, distanceEchoR])

try:
    sideObstacle = 10
    
    driving = True
    while driving:
        carDrive = 0
        carSteering = 0
        car.updateDistances()
        # no obstacle in front of car
        if car.distances[1] > 100:
            if car.distances[0] < sideObstacle:
                # turn the car towards the right
                carSteering = 1
                setDrive = 1
            elif car.distances[2] < sideObstacle:
                # turn the car towards the left
                carSteering = -1
                setDrive = 1
        # approaching an obstacle
        elif car.distances[1] > 30:
            # obstacles are closer on the right
            if car.distances[0] > car.distances[2] and car.distances[1] > sideObstacle:
                setSteering = -1
                setDrive = 1
            # obstacles are closer on the left
            elif car.distances[2] > sideObstacle:
                setSteering = 1
                setDrive = 1
            # can't reliably turn
            else:
                setSteering = 0
                setDrive = -1
        else:
            driving = False
        car.setSteering(carSteering, 80)
        car.setDrive(carDrive)

except KeyboardInterrupt:
    pass

car.stop()

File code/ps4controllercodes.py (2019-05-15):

class BTN:
    #Other button control codes
    share = 314
    option = 315
    home = 316

    #Button control codes
    x = 304 # X
    o = 305 # O
    t = 307 # triangle
    s = 308 # square
    left_js = 317 # left joystick 
    right_js = 318 # right joystick

class DPAD:
    #D-Pad control codes
    left_right = 16
    left_code = -1
    right_code = 1
    up_down = 17
    up_code = -1
    down_code = 1

class TRIG:
    #Trigger control codes
    l1 = 310
    l2 = 312
    r1 = 311
    r2 = 313
    hold_l2 = 2
    hold_r2 = 5

class JS:
    #Joystick axis codes
    left_x = 0
    left_y = 1
    right_x = 3
    right_y = 4

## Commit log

2019-04-11 Added currently used 3d models
    [BracketAxle.stl, LargeGear.stl, RightArm.stl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]
2019-04-18 Added functionality to toggle firing laser/nerf gun.
2019-05-06 Added base rotation with a servo and added angle tracking and verification
2019-05-10 Changed Cannon.py to use pigpio instead of RPi to fix servo issues and fixed a few bugs
    [Cannon.py, CannonTest.py]
2019-05-10 Added instructions for assembling the cannon
2019-05-10 Updated with current 3d models.
    [Arm.stl, ArmAxle.stl, ArmAxleGear.stl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]
2019-05-13 Added Cannon Wiring Diagram
2019-05-13 print coordinates of center of upper body
2019-05-13 fixed printing coordinates
2019-05-13 Renamed stepper motor pin variables
2019-05-13 Minor changes to naming and fixes
    [web.py]
2019-05-13 Fixed some minor bugs
    [tankps4.py]
2019-05-14 Fixed some minor bugs preventing loading
    [web.py]
2019-05-14 Removed an unneeded debugging print statement
2019-05-14 Added multi-threading to run the auto detection in the same program as the webserver and added the ability to switch between manual and automatic modes
2019-05-14 Added some checks to prevent duplicate logs (un tested) Added a video stream from the detection system (also un tested) Possibly other changes/fixes
    [web.py]
2019-05-15 Updated Car class to use pigpio instead of RPi, will be testing pwm speed control
2019-05-15 Fixed a bug with the setCannonPos method
    [Cannon.py]
2019-05-15 Fixed webinterface alignment, add favicon because why not, and some minor changes to the webserver
    [web.py]
2019-05-15 Fixed Car class import and fixed backwards drive control
    [tankps4.py]
2019-05-15 Added pwm speed control to the Car class for the drive and steering motors
2019-05-15 Car class now takes a percent for speed control of motors Can now control the cars speed with the ps4 controller
2019-05-15 Updated web interface to control car drive and steering with speed instead of on/off
2019-05-16 Fixed a bug with setting car steering
    [web.py]
2019-05-17 Fixed an issue with logging found targets and added a loading image to prevent errors when loading the webpage before the stream is ready
    [web.py]
2019-05-17 Fixed an issue with the process hanging when ctrl+c was pressed with a stream running
    [web.py]
2019-05-17 Fixed an issue with the cannon motion caused by threading flask
    [Cannon.py, web.py]
2019-05-17 Cannon going out of sync after long/rapid movements should be fixed now
    [Cannon.py, web.py]
2019-05-23 detection working and print % of red inside body
2019-05-23 added camera des
2019-06-06 camera web link
2019-09-16 Updated the car class to use distance sensors
2019-09-16 Created camerapi.py to be used with pi cameras and updated web.py to work with camerapi. Fixed hanging issues when using ctrl+c to stop the web app.
    [camerapi.py, web.py]
2019-09-17 Changed resolution of the camera to 640x480
2019-10-02 Setup cannon to move based on detected person. -Needs tweaking when car is fixed.
    [Cannon.py, camerapi.py, web.py]
2019-10-12 Added cannon moving/targeting based on camera detection position
2019-10-13 Fixed code for distance sensor reading
    [Car.py, web.py]
